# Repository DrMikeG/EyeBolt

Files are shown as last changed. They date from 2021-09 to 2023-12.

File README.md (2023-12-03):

# EyeBolt #

## 10th September 2023 ##
I've just captured the first full scan on the work driven turntable.
\EyeBolt\Mk5\Code\20_100StepTurnsTakingPictures\run_036

I'm now having a chat with chatGPT about the next steps:
```
`cv2.solvePnP()` is a function provided by the OpenCV library in Python for solving the Perspective-n-Point (PnP) problem, which is used in computer vision to estimate the pose (rotation and translation) of an object in a 3D space relative to a camera. This is precisely what you need when determining the extrinsic parameters between your camera and laser in your 3D scanner project.

Here's a more detailed explanation of how to use `cv2.solvePnP()`:

```python
import cv2
import numpy as np

# Define known 3D world points (object points)
object_points = np.array([
    [x1, y1, z1],
    [x2, y2, z2],
    # ... add more points ...
], dtype=np.float32)

# Define detected 2D image points
image_points = np.array([
    [u1, v1],
    [u2, v2],
    # ... add more points ...
], dtype=np.float32)

# Define camera matrix (intrinsic parameters), obtained from camera calibration
camera_matrix = np.array([
    [fx, 0, cx],
    [0, fy, cy],
    [0, 0, 1]
], dtype=np.float32)

# Define distortion coefficients if applicable (usually from camera calibration)
distortion_coeffs = np.array([k1, k2, p1, p2, k3], dtype=np.float32)

# Use cv2.solvePnP to estimate pose (extrinsic parameters)
retval, rotation_vector, translation_vector = cv2.solvePnP(object_points, image_points, camera_matrix, distortion_coeffs)

# 'retval' indicates the success of the solvePnP operation (usually 1 if successful)

# 'rotation_vector' is the rotation in Rodrigues form (axis-angle representation)
# Convert it to a rotation matrix if needed
rotation_matrix, _ = cv2.Rodrigues(rotation_vector)

# 'translation_vector' represents the translation of the object center in camera coordinates

# The resulting 'rotation_matrix' and 'translation_vector' represent the pose of the object
```

Key points to note:

- You need to provide `object_points`, which are the 3D coordinates of known points in the world coordinate system.
- `image_points` are the 2D coordinates of the corresponding points in the image.
- `camera_matrix` is the camera's intrinsic matrix, obtained through camera calibration.
- `distortion_coeffs` are the distortion coefficients, also obtained from camera calibration (may not always be needed).

The function returns the rotation vector (`rotation_vector`) and translation vector (`translation_vector`) that describe the pose of the object in relation to the camera.

You can then use the rotation and translation information to transform your laser line data from the camera's coordinate system to the world coordinate system, allowing you to align the laser data with your 3D point cloud.

Remember to make sure that your world points and image points are correctly matched and correspond to the same features in your images for accurate pose estimation. Additionally, if you have lens distortion, it's important to account for it using the distortion coefficients.
```

Measurements of box:
Camera focal plane to far wall distance = 315mm
11cm from far wall to pivot
Camera focal plane to pivot = 315mm - 110mm = 205mm
Blue laser source to camera axis - 92mm
Red laser source to camera axis - 92mm

Blue laser plane:
Origin (-92,0,0)
Direction ()
Vector in plane up far wall - from bottom to top of visible line
Vector in plane run from origin to 

## 4th September 2023 ##
Having mounted the df robot stepper with the 1:100 gearbox, I'm still struggling to get a consistent rotation.

Using the code in 19_QuarterTurnsTakingPictures I'm estimating the error by photographing each rotation and looking for the procession.

The closest I have so far is 1981 steps per revolution, which I still think might be ~2% to much

But the noise is annoying me now, so I'm going to stop.

## 22nd July 2023 ##

Capturing some light and dark rotations today to help debug the point cloud work I've been doing in Open3d (14_Open3d_Tut)

Try one capture after another, and looking at the light rotations, I think 128 steps is more than a full rotation. 122 seems much closer.

Also, my dark captures seem too dark now.

I've stated 15_Capture360_DarkOrLight to allow me to easily change between the new dark/light settings I am trying.

Still working on processing in Mk5\Code\14_Open3d_Tut\02_make_point_cloud_file.py
which can now:
- Make an undistorted light or dark frame video
- Make a side-by-side light and dark frame video (needs orientation to line up)
- Make a file containing point cloud coordinates from dark frames
- Display a point cloud using open3D

(The difference between light frames and dark frames is just me opening or closing the box... he he)

I'm not convinced by the settings in 
\EyeBolt\Mk5\Code\15_Capture360_DarkOrLight\my_camera_light.py
\EyeBolt\Mk5\Code\15_Capture360_DarkOrLight\my_camera_dark.py

Having some success processing light frames.

I should diagnose the turning issue by doing 1 photo per revolution for 10 revs...

## 13th July 2023 ##

Where are we up to?
I'm now capturing runs of cropped 950x950 images with low noise.
This took a lot of messing - but I'm very please with the result.

## 8th July 2023 ##

Because of the field of view, I don't care about much of the image.
Pico has limit - Max 150kb of data
Ideally I'd like 1.5mb for 900x900 at full resolution - but equally I don't care about most of the those pixels, only the red ones.

Most experiments with 2560x1440 at high compression (24)
Binning is automatically enabled when output size is less 1440, so wondered where many of my pixels went when I used small output.

The library I am using is really useful for setting the 100s of registers and capturing the output data.
But output size is set using an enum indexing into a table.

I didn't really want to abandoned the library, since its setting dozens of useful register values, but I want to use an output format that's not one of the pre-canned enum rows in the table.

The library itself is compiled into binary for efficiency, so I can't change it - but it turns out the table values are read-write so I can overwrite one row in the table.

I started off copying all the values from a working row, and setting the offsets to shuffle a cropped window along.

The camera works in two modes depending on the output size - so the values are used differently depending, which took me a while to figure out.

With a bit of trial and error, managed to shift the capture window the be 950x950 (without scaling?)

Capturing fewer pixels allowed me to lower the compression from 24 to 6 (very close to 5)

The next issue to address is the noise.
The library is very video-focused and doesn't expose any of the setting related to the auto-exposure or auto-gain controls.

Here I have to go to the data sheet and start messing with individual bits in registers.

My approach here was to set the camera to a known good state, take a photo, then adjust some experimental settings, and take a second photos and compare.

## 7th July 2023

Following other leads on long exposure:

https://forums.openmv.io/t/need-help-with-ov5640-exposure-timing/8238/5
https://forums.raspberrypi.com/viewtopic.php?t=350473

## 3rd July 2023 ##
Seem to have lost this link.
https://github.com/espressif/esp32-camera/issues/203

https://github.com/espressif/esp32-camera/blob/master/sensors/ov5640.c

## 2nd July 2023 ##

- If width is less than half of max width or height is less than half of max height then enable binning by setting _binning to be true
Further settings are the specified within _set_image_options()

- If width and height are equal to max width and max height then we don't need to scale, set _scale to false
- If width and height are equal to half max width and half max height then we don't need to scale if we using binning, set _scale to false
- Else we are using scaling:  `self._write_reg_bits(_ISP_CONTROL_01, 0x20, self._scale)` - this is using a mask to set the 5th bit

Other than the `_ISP_CONTROL_01 (0x5001) - # Bit[5]: Scale enable 0: Disable 1: Enable`
I don't see anything that sets scaling, and nothing uses the defined scaling registry addresses.

If you enable the value in this register, I think it must interpret the values X_OUTPUT_SIZE and Y_OUTPUT_SIZE differently.
X_OFFSET sn Y_OFFSET are used to define the copy before scaling and X_OUTPUT_SIZE and Y_OUTPUT_SIZE defined the scaled image size.

So, for the output size OV5640_SIZE_QHD (# 2560x1440)
h,      w,      mw,     mh,     sx, sy,     ex,     ey,     ox, oy, tx,     ty
2560,   1440,   2560,   1440,   0,  240,    2623,   1711,   32, 16, 2844,   1488, # QHD

```
self._binning = false # (1440 <= 1440 // 2) and (height <= max_height // 2)
self._scale = false # not ((true and true)

self._write_addr_reg(_X_ADDR_ST_H, 0, 240)
self._write_addr_reg(_X_ADDR_END_H, 2623, 1711)
self._write_addr_reg(_X_OUTPUT_SIZE_H, 2560, 1440)

self._write_addr_reg(_X_TOTAL_SIZE_H, 2844, 1488)
self._write_addr_reg(_X_OFFSET_H, 32, 16)

self._write_reg_bits(_ISP_CONTROL_01, 0x20, self._scale)
```

Thinking about moving away from jpeg again.
Example gif code:
``` 
frame = wait_record_pressed_update_display(True, cap)
    with open_next_image("gif") as f, gifio.GifWriter(
        f, cam.width, cam.height, displayio.Colorspace.RGB565_SWAPPED, dither=True
    ) as 
        ```

https://docs.circuitpython.org/en/latest/shared-bindings/gifio/index.html

file – Either a file open in bytes mode, or the name of a file to open in bytes mode.

width – The width of the image. All frames must have the same width.

height – The height of the image. All frames must have the same height.

colorspace – The colorspace of the image. All frames must have the same colorspace. The supported colorspaces are RGB565, BGR565, RGB565_SWAPPED, BGR565_SWAPPED, and L8 (greyscale)

The GIF frames are decoded into RGB565 big-endian format. displayio expects little-endian, so the example above uses Colorspace.RGB565_SWAPPED.

https://learn.adafruit.com/saving-bitmap-screenshots-in-circuitpython/overview
```
This guide introduces a CircuitPython library which is compatible with CircuitPython 5.0 and later. The library allows the programmer to take the pixels in a bitmap or on a screen and save them into standard 24 bits per pixel BMP files. Files may be on the CircuitPython USB flash filesystem (if it's set to writable mode) or onto a SD card.

To save bitmaps and screenshots you will need to add adafruit_bitmapsaver.mpy to the CIRCUITPY/lib directory.

save_pixels('/sd/pypaint.bmp', self._fg_bitmap, self._fg_palette)
```
http://paulbourke.net/dataformats/ppm/

## 1st July 2023 ##
In my v12 code to TweakCameraSettings I am using cam._write_register()

If I want to check current values I should try _read_register()

Looking at the internals we have a method on OV5640:
```
 def _set_size_and_colorspace(self) -> None:  # pylint: disable=too-many-locals
        
        # I am using  size=adafruit_ov5640.OV5640_SIZE_QHDA = 14  # 2560x1440
        size = self._size
        # [2560, 1440, _ASPECT_RATIO_16X9], # QHD
        # _ASPECT_RATIO_16X9 = const(4)
        width, height, ratio = _resolution_info[size]
        # _ratio_table = [
        #  mw,   mh,  sx,  sy,   ex,   ey, ox, oy,   tx,   ty
        #[2560, 1440, 0, 240, 2623, 1711, 32, 16, 2844, 1488],  # 16x9
        #]

        self._w = width     # 2560
        self._h = height    # 1440
        (
            max_width,      # 2560
            max_height,     # 1440
            start_x,        # 0
            start_y,        # 240
            end_x,          # 2623
            end_y,          # 1711
            offset_x,       # 32
            offset_y,       # 16
            total_x,        # 2844
            total_y,        # 1488
        ) = _ratio_table[ratio]

        self._binning = (width <= max_width // 2) and (height <= max_height // 2)
        self._scale = not (
            (width == max_width and height == max_height)
            or (width == max_width // 2 and height == max_height // 2)
        )

        self._write_addr_reg(_X_ADDR_ST_H, start_x, start_y)
        self._write_addr_reg(_X_ADDR_END_H, end_x, end_y)
        self._write_addr_reg(_X_OUTPUT_SIZE_H, width, height)

        if not self._binning:
            self._write_addr_reg(_X_TOTAL_SIZE_H, total_x, total_y)
            self._write_addr_reg(_X_OFFSET_H, offset_x, offset_y)
        else:
            if width > 920:
                self._write_addr_reg(_X_TOTAL_SIZE_H, total_x - 200, total_y // 2)
            else:
                self._write_addr_reg(_X_TOTAL_SIZE_H, 2060, total_y // 2)
            self._write_addr_reg(_X_OFFSET_H, offset_x // 2, offset_y // 2)

        self._write_addr_reg(_X_TOTAL_SIZE_H, total_x - 200, total_y // 2)
        self._write_addr_reg(_X_OFFSET_H, offset_x // 2, offset_y // 2)

        self._write_reg_bits(_ISP_CONTROL_01, 0x20, self._scale)
```
mw	2560				
mh	1440				
sx	0	_X_ADDR_ST_H			
sy	240	_X_ADDR_ST_H			
ex	2623	_X_ADDR_END_H			
ey	1711	_X_ADDR_END_H			
ox	32	_X_OFFSET_H	If not binning	16	_X_OFFSET_H
oy	16	_X_OFFSET_H	If not binning	8	_X_OFFSET_H
tx	2844	_X_TOTAL_SIZE_H	If not binning	2644	
ty	1488	_X_TOTAL_SIZE_H	If not binning	744	
scale	0	_ISP_CONTROL_01	0x20		

```
def _write_addr_reg(self, reg: int, x_value: int, y_value: int) -> None:
        self._write_register16(reg, x_value)
        self._write_register16(reg + 2, y_value)
```

There are two different window configurations, depending on if scaling is enabled.

The values above don't appear to make sense. What registers are they going into?

The OV5640 sensor has an image array of 2624 columns by 1964 rows
Of the 5,153,536 pixels, 5,038,848 (2592x1944) are active pixels and can be output. The other pixels are used for black 
level calibration and interpolation.

## 30th June 2023 ##
![manual](./readme_imgs/bit_packing_01.png)

The 8 bits of register 0x3821 control multiple things:
- jpeg enabled
- isp mirror
- sensor mirror
- horizontal binning

When setting the windowing, I will need to or in my additional bits.

The OV5640 using registers 0x3800 -> 0x3814 for image windowing.
(but maybe not all the bits)

| Address    | Register Name     | Default Value | Description                             |
|------------|-------------------|---------------|-----------------------------------------|
| OX3800     | TIMING HS         | 0x00          | X address start high byte[ll:8] high byte |
| OX3801     | TIMING HS         | 0x00          | X address start low byte[7:0] low byte |
| OX3802     | TIMING VS         | 0x00          | Y address start high byte[10:8] high byte |
| OX3803     | TIMING VS         | 0x00          | Y address start low byte[7:0] low byte |
| OX3804     | TIMING HW         | 0x0A          | X address end high byte[11:8] high byte |
| OX3805     | TIMING HW         | 0x3F          | X address end low byte[7:O] low byte |
| OX3806     | TIMING VH         | 0x07          | Y address end high byte[10:8] high byte |
| OX3807     | TIMING VH         | 0x9F          | Y address end low byte[7:O] low byte |

DVP - Digital video port parallel output interface
```The Digital Video Port (DVR) provides 10-bit parallel data output in all formats supported and extended features including 
compression mode, HSYNC mode, CClR656 mode, and test pattern output. The DVP is also used to receive the video 
data from an external camera, which will be sent out through the OV5640 MIPI interface. ```

| OX3808     | TIMING DVPHO      | 0x0A          | DVP output horizontal width[ll:8] high byte|
| OX3809     | TIMING DVPHO      | OX20          | DVP output horizontal width[7:0] low byte |
| OX380A     | TIMING DVPVO      | OX07          | DVP output vertical height[10:8] high byte |
| OX380B     | TIMING DVPVO      | OX98          | DVP output vertical height[7:0] low byte |
| OX380C     | TIMING HTS        | 0x0B          | Total horizontal size[ll high byte |
| OX380D     | TIMING HTS        | 0x1C          | Total horizontal size[7:0] low byte |
| OX380E     | TIMING VTS        | 0x07          | Total vertical size[1 5:8] high byte |
| OX380F     | TIMING VTS        | 0xB0          | Total vertical size[7:0] low byte |
| OX3810     | TIMING HOFFSET    | 0x00          | ISP horizontal offset[ll :8] high byte |
| OX3811     | TIMING HOFFSET    | 0x10          | ISP horizontal offset[7:0] low byte |
| OX3812     | TIMING VOFFSET    | 0x00          | ISP vertical offset[10:8] high byte  |
| OX3813     | TIMING VOFFSET    | 0x04          | ISP vertical offset[7:0] low byte  |

From the manual:

+------------------+--------------+-----------+------------------------------------+----------------+
|      Format      | Resolution   | Frame Rate|         Scaling Method             |  Pixel Clock   |
+------------------+--------------+-----------+------------------------------------+----------------+
|    5 Mpixel      |  2592X1944   |   15 fps  |   Full resolution (dummy 16 pixels, |   96/192 MHz   |
|                  |              |           |   horizontal, 8 lines)             |                |
+------------------+--------------+-----------+------------------------------------+----------------+
|    1280X960      |  1280X960    |   45 fps  |   2608x1952 with dummy              |   96/192 MHz   |
|                  |              |           |   subsampling in vertical and       |                |
|                  |              |           |   horizontal                        |                |
+------------------+--------------+-----------+------------------------------------+----------------+
|    1080P         |  1920X1080   |   30 fps  |   1296X968                          |   96/192 MHz   |
+------------------+--------------+-----------+------------------------------------+----------------+
|    720P          |  1280X720    |   60 fps  |   Supports 2x2 binning              |   96/192 MHz   |
+------------------+--------------+-----------+------------------------------------+----------------+
|    VGA           |  640X480     |   90 fps  |   Cropping from full resolution     |   48/96 MHz    |
|                  |              |           |   (1936x1088 with dummy pixels)     |                |
+------------------+--------------+-----------+------------------------------------+----------------+
|    QVGA          |  320X240     |   120 fps |   Cropping 2592x1944 to 2560x1440   |   24/48 MHz    |
|                  |              |           |   Subsampling in vertical and       |                |
|                  |              |           |   horizontal                        |                |
+------------------+--------------+-----------+------------------------------------+----------------+

## 29th June 2023 ##
Using code 11 I tried lots of different camera settings. There were better and worse settings, but none of them I would say were good, and there were lots of errors.
The errors might be the result of me changing the settings to frequently.

## 15th June 2023 ##
Lets look at how I could capture higher quality in less memory.

https://docs.python.org/3/c-api/buffer.html#bufferobjects

## 4th June 2023 ##
Adding SD card to camera module to aid calibration.

I want high quality images - going to try writing from camera to SD card.

06_ will mix together 04_largeBitmapCapture with protoMicroSDWithMotor.

Additional libs:
adafruit_sdcard.mpy which I've taken from adafruit-circuitpython-bundle-7.x-mpy-20230325

Saving images at SXGA (1280x1024)
Quality - Controls the JPEG quality.  Valid range is from 2..55 inclusive

Quality 4
1280 1024
327680
Traceback (most recent call last):
  File "code.py", line 193, in <module>
  File "code.py", line 164, in main
MemoryError: memory allocation failed, allocating 327680 bytes

## 24th May 2023 ##
Camera calibration

Give me an overview of how to perform OpenCV's cv2.calibrateCamera function.
https://docs.opencv.org/4.x/dc/dbb/tutorial_py_calibration.html

Instead of chess board, we can alternatively use a circular grid. In this case, we must use the function cv.findCirclesGrid() to find the pattern. Fewer images are sufficient to perform camera calibration using a circular grid.

https://longervision.github.io/2017/03/18/ComputerVision/OpenCV/opencv-internal-calibration-circle-grid/

## 23rd May 2023 ##

Micro SD cards.

I can't keep sending image data across the serial terminal - it's madness. Maybe once I have the processing algorithm dialed in I can put it back on the pico, but to start with, I think I want to capture a load of full res- images.

I plan to add a micro SD card reader to the pico.
I had one in my box of bits, but it was a generic one, which didn't look like it could use `sdcardio`.

I bought an Adafruit MicroSD Card breakout+ (P254)
https://www.adafruit.com/product/254

This has the DI and DO pins, so I should be able to follow this guide: https://learn.adafruit.com/adafruit-micro-sd-breakout-board-card-tutorial/circuitpython

I don't so the pi pico on the list, so cannot verify that it supports sdcardio. If it does not, I will try using adafruit_sdcard instead.

Wiring: https://learn.adafruit.com/adafruit-micro-sd-breakout-board-card-tutorial/arduino-wiring

Because SD cards require a lot of data transfer, they will give the best performance when connected up to the hardware SPI pins.

SPI Example
To setup a SPI bus, you specify the SCK, MOSI (microcontroller out, sensor in), and MISO (microcontroller in, sensor out) pins. 
The Pico uses a different naming convention for these:

SPIx_SCK = SCK
SPIx_TX = MOSI
SPIx_RX = MISO
So use that mapping to help find available pins.

import board
import busio
spi = busio.SPI(clock=board.GP2, MOSI=board.GP3, MISO=board.GP4)

This clashes with the pins I've used for the motor so far, so I will need to re-prototype that.

Connect the 5V pin to the 5V pin on the Arduino
Connect the GND pin to the GND pin on the Arduino

Connect (Brown) CLK to pin 13 SCK (SPIx_SCK) clock=board.GP2
Connect (Orange) DO to pin 12 MISO (SPIx_TX) MISO=board.GP4
Connect (Yellow) DI to pin 11 MOSI (SPIx_RX ) MOSI=board.GP3
Connect (Green) CS to pin 10 (you will also need a fourth pin for the 'chip/secondary select' (SS))

`Go to the beginning of the sketch and make sure that the chipSelect line is correct, for this wiring we're using digital pin 10 so change it to 10!`
`Use 8.3 format for file names`

Soldered up the wires and connecting to a pico on a protoboard.
Copied across library adafruit_sdcard.mpy which I've taken from adafruit-circuitpython-bundle-7.x-mpy-20230325

Edited the file list example into \Mk5\Code\protoMicroSD - run it and listed the files on the SD card.

Next test is to write a file - and generate unique filename in 8.3

I have to move the motor now too, as that was overlapping with the SPI pins.
I don't think it needed to.

```
import board
import busio
import sdcardio
import storage
# Use the board's primary SPI bus
spi = board.SPI()
# Or, use an SPI bus on specific pins:
#spi = busio.SPI(board.SD_SCK, MOSI=board.SD_MOSI, MISO=board.SD_MISO)

# For breakout boards, you can choose any GPIO pin that's convenient:
cs = board.D10
```

Another quick experiment in \Mk5\Code\protoMicroSDWithMotor

Moved motor pins to 6,7,8 & 9. This works, but that now clashes with 7,8 & 9 being used by the camera!

I've managed to move to the motor to 22,26,27 & 28.

That leaves my GP6 free for E-brake, and maybe 0 and 1 - but I never like using them.

## 30th April 2023 ##

First light?

OV5640_COLOR_RGB = 0
OV5640_COLOR_YUV = 1
OV5640_COLOR_GRAYSCALE = 2
OV5640_COLOR_JPEG = 3
https://github.com/adafruit/Adafruit_CircuitPython_OV5640/blob/main/adafruit_ov5640.py

OV5640_SIZE_96X96 = 0  # 96x96
OV5640_SIZE_QQVGA = 1  # 160x120
OV5640_SIZE_QCIF = 2  # 176x144
OV5640_SIZE_HQVGA = 3  # 240x176
OV5640_SIZE_240X240 = 4  # 240x240
OV5640_SIZE_QVGA = 5  # 320x240
OV5640_SIZE_CIF = 6  # 400x296
OV5640_SIZE_HVGA = 7  # 480x320
OV5640_SIZE_VGA = 8  # 640x480
OV5640_SIZE_SVGA = 9  # 800x600
OV5640_SIZE_XGA = 10  # 1024x768
OV5640_SIZE_HD = 11  # 1280x720
OV5640_SIZE_SXGA = 12  # 1280x1024
OV5640_SIZE_UXGA = 13  # 1600x1200
OV5640_SIZE_QHDA = 14  # 2560x1440
OV5640_SIZE_WQXGA = 15  # 2560x1600
OV5640_SIZE_PFHD = 16  # 1088x1920
OV5640_SIZE_QSXGA = 17  # 2560x1920

https://github.com/adafruit/Adafruit_CircuitPython_BitmapSaver
https://learn.adafruit.com/circuitpython-display-support-using-displayio/bitmap-and-palette

https://cdn-learn.adafruit.com/assets/assets/000/118/553/thumb100square/adafruit_products_img0006.jpg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

## 19th April 2023 - Mark V progress ##

I've been working on this perhaps more than I realise.
So, a quick video to capture the changes.

I set out to test the camera - which means wiring up the camera board.
But before did that, I decided I wanted to test the other features of the board, which in this design means control of the turn table.

I start out with the parts I stripped out of the mark 4.
I used the Tb6612 motor control board, with the beefy 12volt nema 17 motor.

I made a timing belt driven system where a 20 tooth gear on the motor drives a 400 tooth belt around the outside of this 3d printed turntable.
This gives me 1800 steps per revolution - but it was noisy and a bit rough.

In the previous design I had one motor turning a pair of chunk lead screws - pushing assemblies along a pair of linear rails. It needed some grunt.

But here, I'm just spinning a table in free space - no grunt needed. So i've switch down a litte 5v 28BYJ geared stepper. This gives me 512 steps be revolution and is buttery smooth and silent.

In other news, I've started to mount the components in their box.

I'm just 3d printing frame sections, that clip over the rim of the box, and align the content to be vertical.

Here I have the camera board and pico mounted on a protoboard (which is not yet wired) And I have the Powell lense laser tacked on the end.

I'm thinking I should make the turn table attach to this, to make a single unit, rather than fixing it to the box. This would make allow me to make a CAD model of the whole assembly, rather than try to measure it accurately.

Not sure about that yet.

Next steps? Well, Now I've proven I can drive the turn table, I should start wiring up nthe camera and try to get a first image.

Nema 17 = 200 steps per revolution
20 tooth cog, so 10 steps per tooth.
Driving a 180 tooth table, to 1800

## 14th April 2023 - Stepper trouble ##
I'm reducing the number of stepper motors from 2 to 1.
I only need a motor to driver the turntable.

I've made a motor and table assembly with a 400 tooth 2gt timing belt. Small gear has 20 teeth and large gear has 180.

I'm struggling to get any motor to run smoothly and reliably. I've switch out motor driver boards and nema 17 motors. It's all very rattly.

Since there is almost no load on this motor, I'm considering switching down to a tiny 28byj-48, 5V stepper.

https://microcontrollerslab.com/28byj-48-stepper-motor-raspberry-pi-pico-micropython/

https://forums.adafruit.com/viewtopic.php?f=19&t=117680

I also found a suggestion for diagnosing the control lines, so I might try that first too.

## 10th April 2023 - Wiring up camera protoboard ##
I have a protoboard for the pico from Monk makes

![PICO PROTO PCB](./readme_imgs/monk.jpg)

Which seems perfect for this wiring job. I have the camera on via a socket and the pico soldered directly on board.

I have a 5v 3v3 and Gnd rail, and the camera pins are broken out onto columns, which should make is easy for me to solder them.

My next question, is do I have 5 spare pins for the motor board?

Whilst I print test-support pieces to interface the camera board and the prototboard, I'm thinking about the new turn table:

https://avtehnik.github.io/gt2-gear-genaretor/

Using a 140 tooth turntable, using a belt length tool:

https://www.technobotsonline.com/timing-pulley-distance-between-centres-calculator.html

140 on larger PCD (dp) 89.127
20 on smaller PCD (dp) 12.732
Distance between centers 113.577
Belt length 400mm

## 8th April 2023 - Start of the Mark V ##

Adafruit OV5640 Camera Breakout - 120 Degree Lens
https://learn.adafruit.com/adafruit-ov5640-camera-breakout/raspberry-pi-pico-usage

Camera connections
For the Raspberry Pi Pico setup shown in these examples, wire the following connections:

OV5640 GND to Pi Pico GND
OV5640 3V to Pi Pico 3V3
OV5640 SDA to Pi Pico GP8
OV5640 SCL to Pi Pico GP9
OV5640 HS to Pi Pico GP21
OV5640 VS to Pi Pico GP7
OV5640 XC to Pi Pico GP20
OV5640 PC to Pi Pico GP11
OV5640 D2..D9 to Pi Pico GP12..GP19
OV5640 RT to Pi Pico GP10

The pull-up resistors shown on GP8 and GP9 are not required for Adafruit's OV5640 camera break-out board but may be required for other camera breakout boards.

![Alt text](./readme_imgs/adafruit_products_5673-fb.jpg)

![Alt text](./readme_imgs/adafruit_products_pico-camera-lcd_bb.png)

The camera module requires a well-regulated 3.3v supply in order to operate.

**G (GND):** Connect to microcontroller GND

**3V (3.3V):** Connect to microcontroller +3.3V supply

PD (powerdown): Optional connection to microcontroller GPIO. When pulled HIGH the camera module is put into power-down mode. When released or pulled LOW the camera is powered on. This pin can also be pulsed HIGH as a way to reset the camera.
RT (reset): Optional connect to microcontroller GPIO. Pull the pin LOW to reset the camera module and release it or pull it HIGH to enter operating mode.
Both pins have built-in pull resistors, so by default the camera is powered on and allowed to exit reset mode.

The camera module must be configured using I2C.

**SDA:** Connect to microcontroller SDA

**SCL:** Connect to microcontroller SDL

**XC (external clock)**: When the XCLK jumper is set to "EXT" (the default), this pin must be driven with a 24MHz square wave from the microcontroller or other source. When the jumper is changed to "INT", then an on-board clock generator is used instead. In this case, the XC pin should not be driven by the microcontroller and may be left unconnected.

**PC (pixel clock)** tells the microcontroller when image data is available. This may need to be connected to a specific microcontroller pin.

**VS and HS** are synchronization signals, which tell the microcontroller when a new frame (VS) or row (HS) of data begins. These may need to be connected to specific microcontroller pins.

The 8 data pins (numbered from **D2 to D9** because reasons) carry data out of the camera into the microcontroller.

Depending on mode, these 8 data bits can be half of a 16-bit pixel value, or one byte of JPEG data.

```If your microcontroller has a 2x9 header available, that method is strongly preferred! The high speed signals of the camera module can be scrambled even with short lengths of jumper wire on a solderless breadboard.```

xclk, pclk, vsync, href: Free choice of any pin
reset, shutdown: Free choice of any pin. Can omit one or both, but the initialization sequence is less reliable.
data_pins: Any 8 sequential pins in GPIO ordering (e.g., GPIO2..GPIO9).

https://learn.adafruit.com/adafruit-ov5640-camera-breakout/ascii-mirror-dem

## 1st April 2023 - The End of the Mark IV ##

This project has been on pause for a while, whilst I've done other things - but it's very literally always there - taking up space in my study.

This is the Mark 4 - it's a laser beam scanner. There are a pair of synchronized lead-screws, which move the laser and the sensor horizontally along these sturdy linear tracks.

The subject is placed on a linear rotary turntable. Combing the movement of the laser sensor with the 2 degrees of freedom of the table, you can gather 3D data from the occlusion of the data.

Both the table and the lead screws are driven by Nema steppers, the lead screws are synchronized via timing belts, and the turntable is driven via a 3d printed gear pair. Stepper driver boards are controlled by a pico, which coordinates the movement with the sensing.

I've got this built out as far as calibration - and partly looking at those results I've decided not to take this build any further.

The problems are:

1) Too many movement parts.
There's too much slop in the system. Just calibrating this with m2 machine screws, I'm seeing 1mm of inaccuracy on the position, which isn't going to give me the results I want.

2) Too big.
I was a little ambitious with my scan volume
I was limited height-wise by by my turntable design
I was limited length-wise by not wanting to cut up the lead screws and linear rails.
So I build this into this big crate - which isn't something I want to have hanging around (like it has for the past year).

## 11th September 2022 ##

Something I was reader referred to circuitPython AsyncIO - which I don't think was a thing back when I started this project 2 years ago.

This isn't preemptive multi-tasking, but cooperative. You can't break into the event loop following an interrupt, but one task can cede control (let other tasks run) when it is waiting (e.g time.sleep)

This might be a good way forward for me, to try and keep the motor movement fluid. At the moment there are sleep statements in every motor step.

Potentially I could be checking the abort button and the laser sensor whilst the motors are paused.

I'm going to have a play with tis code in Mk4\Code\AsyncIO\Prototype01\code.py

Guide here: <https://learn.adafruit.com/cooperative-multitasking-in-circuitpython-with-asyncio>

```
# SPDX-FileCopyrightText: 2022 Dan Halbert for Adafruit Industries
#
# SPDX-License-Identifier: MIT

import asyncio
import board
import digitalio

async def blink(pin, interval, count):
    with digitalio.DigitalInOut(pin) as led:
        led.switch_to_output(value=False)
        for _ in range(count):
            led.value = True
            await asyncio.sleep(interval)  # Don't forget the "await"!
            led.value = False
            await asyncio.sleep(interval)  # Don't forget the "await"!
        # These tasks finish whenever the for-loop expires

async def main():
    led1_task = asyncio.create_task(blink(board.D1, 0.25, 10))
    led2_task = asyncio.create_task(blink(board.D2, 0.1, 20))

    await asyncio.gather(led1_task, led2_task)  # Don't forget "await"!
    print("done")

asyncio.run(main())
```

What about sharing memory between tasks?

```
# SPDX-FileCopyrightText: 2022 Dan Halbert for Adafruit Industries
#
# SPDX-License-Identifier: MIT

import asyncio
import board
import digitalio
import keypad

class Interval:
    """Simple class to hold an interval value. Use .value to to read or write."""

    def __init__(self, initial_interval):
        self.value = initial_interval

async def monitor_interval_buttons(pin_slower, pin_faster, interval):
    """Monitor two buttons: one lengthens the interval, the other shortens it.
    Change interval.value as appropriate.
    """
    # Assume buttons are active low.
    with keypad.Keys(
        (pin_slower, pin_faster), value_when_pressed=False, pull=True
    ) as keys:
        while True:
            key_event = keys.events.get()
            if key_event and key_event.pressed:
                if key_event.key_number == 0:
                    # Lengthen the interval.
                    interval.value += 0.1
                else:
                    # Shorten the interval.
                    interval.value = max(0.1, interval.value - 0.1)
                print("interval is now", interval.value)
            # Let another task run.
            await asyncio.sleep(0)

async def blink(pin, interval):
    """Blink the given pin forever.
    The blinking rate is controlled by the supplied Interval object.
    """
    with digitalio.DigitalInOut(pin) as led:
        led.switch_to_output()
        while True:
            led.value = not led.value
            await asyncio.sleep(interval.value)

async def main():
    interval1 = Interval(0.5)
    interval2 = Interval(1.0)

    led1_task = asyncio.create_task(blink(board.D1, interval1))
    led2_task = asyncio.create_task(blink(board.D2, interval2))
    interval1_task = asyncio.create_task(
        monitor_interval_buttons(board.D3, board.D4, interval1)
    )
    interval2_task = asyncio.create_task(
        monitor_interval_buttons(board.D5, board.D6, interval2)
    )

    await asyncio.gather(led1_task, led2_task, interval1_task, interval2_task)

asyncio.run(main())
```

This is perhaps a better way to go? Using countio as a layer over interupts?

```
import asyncio
import board
import countio

async def catch_interrupt(pin):
    """Print a message when pin goes low."""
    with countio.Counter(pin) as interrupt:
        while True:
            if interrupt.count > 0:
                interrupt.count = 0
                print("interrupted!")
            # Let another task run.
            await asyncio.sleep(0)

async def main():
    interrupt_task = asyncio.create_task(catch_interrupt(board.D3))
    await asyncio.gather(interrupt_task)

asyncio.run(main())
```

Inside the interrupt, I'd want to know the current value of X, and have someone to stash it.
We could clear and reset the values for each sweep.

Here main() is run with asyncio - I think I would need other tasks
Task per sweep?

## 6th September 2022 ##

A long line - but not too long.

Powell lenses are laser line generator lens that can fan out collimated beams in one dimension. They have the shape of a prism with a rounded roof, and are often used to transform a narrow laser beam into a uniformly illuminating line. 

If it has a 60 degree beam angle from a 7mm aperture, then at 30cm the beam length is huge.
If I reduce the aperture to 2.6mm then I should get around a 10cm line length at 30cm throw.

## 26th August 2022 ##
Calibrating using the long edge of the L-shaped print.

Zeroing X out at 0
Zeroing X (from 0)
Loop 0 of 10
Detect changed at 1800
Detect changed at 5650
Detect changed at 5630
Detect changed at 1780
Loop 1 of 10
Detect changed at 1800
Detect changed at 5650
Detect changed at 5630
Detect changed at 1780
Loop 2 of 10
Detect changed at 1800
Detect changed at 5650
Detect changed at 5630
Detect changed at 1780
Loop 3 of 10
Detect changed at 1800
Detect changed at 5650
Detect changed at 5630
Detect changed at 1770
Loop 4 of 10
Detect changed at 1800
Detect changed at 5660
Detect changed at 5640
Detect changed at 1780
Loop 5 of 10
Detect changed at 1810
Detect changed at 5660
Detect changed at 5690
Detect changed at 5710
Detect changed at 5640
Detect changed at 1780
Loop 6 of 10
Detect changed at 1800
Detect changed at 5650
Detect changed at 5640
Detect changed at 1780
Loop 7 of 10
Detect changed at 1810
Detect changed at 5650
Detect changed at 5630
Detect changed at 1780
Loop 8 of 10
Detect changed at 1800
Detect changed at 5660
Detect changed at 5700
Detect changed at 5710
Detect changed at 5630
Detect changed at 1780
Loop 9 of 10
Detect changed at 1800
Detect changed at 5650
Detect changed at 5630
Detect changed at 1780
Done!

Detect changed at 1800	1800	1800	1800	1800	1800	1810	1800	1810	1800	1800	1802	
Detect changed at 5650	5650	5650	5650	5650	5660	5660	5650	5650	5660	5650	5653	3851
Detect changed at 5630	5630	5630	5630	5630	5640	5640	5640	5630	5630	5630	5633	
Detect changed at 1780	1780	1780	1780	1770	1780	1780	1780	1780	1780	1780	1779	3854

Between 38.51 and 38.4mm
Measures 39.8

## 21st August 2022 ##

Have been away for two weeks. Just before I left I was working on calibrating the leadscrew movement.

After discovering I could focus the laser - I now need to determine if it's better to focus on the object or the sensor.

Using \Code\Operating\BeamMovementCalibrate\code3.py

```
I estimate 30mm to be an average of 2770 steps

I think the lead-screw is 2mm for 20 teeth
I think the belt drive is 1:1
The motor is 200 steps per revolution
30mm should be 3000 steps
01mm should be 100 steps
I this suggests the fuzz (region of uncertainty) at each end of my block is 1.15mm

Lengths in mm:
27.7
27.7
27.7
27.7
27.7
27.7
27.6
27.6
27.6
27.5
27.6
27.6
27.7
27.7
27.7
27.7
27.7
27.7
27.8
27.8
Measured length 29.84mm

Error (end to end): 
+/- 2.34
+/- 2.04

Happy with this, and the consistent movement in steps of 10 - how can it be improved?

Is there an offset or a reduction I'm not aware off?
It is the beam width? Can I just compensate for that? Does it always measure small?
```

Running again for 15mm block, whilst I print a 25x40mm block

1351 steps (13.5mm)

01mm should be 100 steps
15mm should be 1500 steps
less because there is an area of uncertainty

On the way back, the numbers as consistently lower, suggesting I could run a pass in both directions and take an average!
How to group the readings when they are s

## 29th July 2022 ##

I've just made a measurement of the number of stepper motor steps needed to complete one table revolution.

I put a pin in the table, so that it broke the beam twice per revolution.
I measure the number of steps in each of the 4 states, and averaged to calculate steps per revolution.

I did two runs with the beam at different positions, to get different length quarters

|blockedA|openA|blockedB|openB|sum        |
|--------|-----|--------|-----|-----------|
|28      |319  |39      |2071 |2457       |
|28      |404  |11      |2051 |2494       |
|27      |404  |13      |2044 |2488       |
|25      |416  |15      |2037 |2493       |
|24      |434  |18      |2030 |2506       |
|22      |422  |21      |2029 |2494       |
|20      |428  |22      |2027 |2497       |
|19      |429  |19      |2029 |2496       |
|20      |428  |18      |2029 |2495       |
|20      |430  |15      |2031 |2496       |
|19      |432  |19      |2024 |2494       |
|19      |437  |19      |2021 |2496       |
|17      |439  |21      |2018 |2495       |
|20      |447  |20      |2014 |2501       |
|12      |450  |22      |2009 |2493       |
|17      |449  |20      |2008 |2494       |
|18      |449  |20      |2003 |2490       |
|19      |455  |20      |2001 |2495       |
|20      |456  |22      |2002 |2500       |
|15      |465  |19      |1997 |2496       |
|18      |463  |17      |1999 |2497       |
|15      |467  |18      |1997 |2497       |
|        |     |        |     |2495.571429|

|blockedA|openA|blockedB|openB|sum        |
|--------|-----|--------|-----|-----------|
|11      |1139 |19      |1330 |2499       |
|19      |1139 |12      |1330 |2500       |
|13      |1139 |12      |1330 |2494       |
|19      |1139 |12      |1316 |2486       |
|19      |1141 |14      |1330 |2504       |
|16      |1140 |13      |1328 |2497       |
|15      |1140 |14      |1327 |2496       |
|15      |1142 |13      |1329 |2499       |
|14      |1138 |13      |1327 |2492       |
|15      |1146 |9       |1329 |2499       |
|15      |1142 |13      |1325 |2495       |
|18      |1140 |12      |1327 |2497       |
|15      |1143 |13      |1324 |2495       |
|17      |1142 |14      |1325 |2498       |
|15      |1142 |15      |1323 |2495       |
|15      |1144 |13      |1327 |2499       |
|14      |1143 |13      |1324 |2494       |
|12      |1145 |15      |1323 |2495       |
|14      |1148 |15      |1322 |2499       |
|10      |1145 |18      |1324 |2497       |
|        |     |        |     |2496.368421|

The gear ratio was designed to be 0.0800 

The motor has a step angle of 1.8deg
360 / 1.8 = 200 steps per revolution.

1.0 / 0.08 = 12.5

200 * 12.5 = 2500.

So the predicted number of steps for a revolution is 2500
The measured is ~2495
If I do 100 sample angles (sounds like a lot) that gives 25 steps per chunk, which feels enough to be accurate without backlash.

## 8th July 2022 ##

I have made a number of modifications to the drive - but I had troubles with the new motor.

The drive speed needed changing, and the wiring colours have changes. I used a breakboard to switch around the wires, having used the trick of spinning the motor by hand and shorting the pairs, to find when the resistance increases.

![Alt text](./readme_imgs/servo_rewire.png)

I have changed from a single belt (with tensioning) to two belts on a double drive gear.

## 11th Jun 2022 ##

### Gearbox ###
Working out a small gear box for the new table design

http://hessmer.org/gears/InvoluteSpurGearBuilder.html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

https://evolventdesign.com/pages/gear-ratio-calculator

Number of Teeth: Input Gear: 20 (16mm diameter)
Number of Teeth: Gear 2:    80 (54mm diameter)
Number of Teeth: Gear 3:    24 (30mm diameter)
Number of Teeth: Gear 4:    75 (80mm diameter)

Gear Ratio:	0.0800

Input Speed:	200
Output Speed:	16.0000

Gears 1 & 2
http://hessmer.org/gears/InvoluteSpurGearBuilder.html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

Gears 3 & 4
http://hessmer.org/gears/InvoluteSpurGearBuilder.html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

![Alt text](./readme_imgs/gears1_2_params.png)
![Alt text](./readme_imgs/gears3_4_params.png)

## Thumbstick ##

I felt like I needed more inputs/controls as I develop the Mk4.

Now that I have more travel, I want to be able to set limits for the scan region (to save time not scanning empty space)

The obvious input formats are up-confirm down-confirm to set the limits of the table (for the height of the part) and left-confirm right confirm to set the limits for the max extent of the part when rotated.

To avoid this input being an awkward series of switch presses, I decided to try and integrate a thumbstick.

The thumbstick from the sensor kit says 5v on the silk screen, but seems to work just fine on 3v3.
It has two analogue outs, which I feed into 26 and 27 (ADC ins on the pico) and a switch which I connect to 22 because it is nearby.

I'm not using the analogue values, only a less than 25% or more than 75% to detect left or right - else it gives no input.

![Alt text](./readme_imgs/thumbA.png)
![Alt text](./readme_imgs/thumbB.png)

I wired it up on a breadboard with a test sketch - then soldered connectors onto the main pico shield.
22, 26 & 27 were thankfully unused. I also spliced on the power lines to the existing 3v3 and ground rows.

I had a bit of trouble wiring 22,26 & 27 and in the end I didn't get the colouring consistent on the thumbstick end and pico end (green and white are swapped).

### Nema no more ###

I thought my old motor might have been:
```Nema 14 Bipolar 1.8deg 5Ncm (7.08oz.in) 0.4A 10V 35x35x20mm 4 Wires```

But it turns out it is probably a:
```Stepper motor - NEMA-17 size - 200 steps/rev, 12V 350mA 20 N*cm,```

My driver (Adafruit TB6612) can handle 1.2A

So I've ordered:

```Nema 17 Bipolar Stepper 1.8deg 12v 1.2A 400mN.m 42x42x40mm 4-wires Nema17 CNC```

This hybrid bipolar Nema 17 stepper motor with 1.8 degree step angle (200 Steps / Revolution).
Manufacturer Part Number: 17HS3001-20B
Motor Type: Bipolar Stepper
Step Angle: 1.8 degree
Holding Torque: 400 mN.m
42.3mm*42.3mm*L40mm

New motor will only be x2 as strong (not x8) but still better. Plus it's a drop in replacement.
I might chose a smaller drive gear. This will mean less tooth contact, but less speed and torque multiplier.

## Mark 3 ##

Starting planning the next major redesign of the scanner - planning on going back to optical - but combination optical/mechanical using occlusion not Time Of Flight.

## KY-008 ##

https://arduinomodules.info/ky-008-laser-transmitter-module/

This module consists of a 650nm red laser diode head, a resistor and 3 male header pins. Handle with caution, do not point the laser beam directly to the eyes.

Operating Voltage	5V

Connect the module signal pin (S) to pin 13 on the Arduino and ground (-) to GND.

The middle pin on the module is not used.

## Receiver ##
Laser Receiver Sensor Module non-modulator Tube Pi Arduino Pic Lazer

The laser receiver sensor module uses a non-modulated laser receiver to detect the laser signal.

For use indoors where there is no light, sunlight or other sources of light which will interfere with the sensor, recommended for use in dark environments.

![Alt text](./readme_imgs/s-l1600.jpg)
 
Voltage : 5v
Output high level when receive laser signal
Output low level when not receive laser signal
Size : 1.5cm x 1.9cm

https://www.codrey.com/electronic-circuits/the-mysterious-laser-receiver-sensor-module/

```
A cryptic 3-pin sensor?
The 3-pin sensor is actually a minuscule light sensor (receiver) diode with an integrated amplifier and an open-collector transistor at its output. Output of the module, designed to operate on 5VDC power supply, can only go low (L), and the open-collector transistor inside the 3-pin sensor can sink about 20mA current. The description “non-modulator tube” actually points the fact that the light sensor can handle any source of light and it’s not like a 3-pin  infrared sensor module (TSOP1838 for example) that only detects an infrared pulse train within a particular frequency band.

...the sensor is known in China as “ISO203 Laser Receiver”. You can see its pin notation in the image provided below.
```

![Alt text](./readme_imgs/sensor2.png)

![Alt text](./readme_imgs/20220330_133722.jpg)
This is going to be so cool!

https://matplotlib.org/stable/gallery/mplot3d/voxels_rgb.html

After dealing with an issue where the ends of the arms bounce after the beginning and end of the stroke, I could start some calibration scans.

![Alt text](./readme_imgs/2022_04_15.gif)

## 9th March 2022 ##

Hit various problems with boundary tracing.
Firstly, had to reduce tracing to 4-connected from 8-connected
Then remove small regions,

Now, with my new spring can scan, I have a boundary on level rev_i == 3 where the path crosses itself:

![Alt text](./readme_imgs/2022_09_03_01.png)

| Chunk  | N     | Steps       | diff |
|----|------|--------|---|
| 71 | 12   | 852   |   |
| 36  | 13   | 458     |   |
| 1  | 13.3 | 13.3   |   |
|108 |      | 1333.3 | 0 |

108
54
27

### Hat Scans ###

![Alt text](./readme_imgs/hat.gif)

![Alt text](./readme_imgs/hatMeasure.gif)

![Alt text](./readme_imgs/sorting_hat_point_cloud.png)

![Alt text](./readme_imgs/2022_09_03_01.png)

![Alt text](./readme_imgs/HatMinBool.png)

## 30th Sept 2021 ##

Push buttons have too much spring.
Can I get a photo interupter to work?
KY-10 <https://arduinomodules.info/ky-010-photo-interrupter-module/>

Connect the power line (middle) and ground (left) to +5V and GND respectively. Connect signal (S) to pin 3 on the Arduino.

Operating Voltage 3.3 ~ 5V

- (left) GND
middle +5V
S (right) Pin 3

```
int Led = 13; // define LED pin
int buttonpin = 3; // define photo interrupter signal pin
int val; //define a numeric variable

void setup()
{
 pinMode(Led, OUTPUT); // LED pin as output
 pinMode(buttonpin, INPUT); //photo interrupter pin as input
}

void loop()
{
 val=digitalRead(buttonpin); //read the value of the sensor 
 if(val == HIGH) // turn on LED when sensor is blocked 
 {
  digitalWrite(Led,HIGH);
 }
 else
 {
  digitalWrite(Led,LOW);
 }
}
```

### Gear Ratio ###

80 : 12
360 / 1.8 = 200 steps per revolution.

200 / 12 = 16.66667
16.66667 * 80 = 1333.33

My measured estimate was 1331
Leap-step every 3 revolutions

## 26th Sept 2021 ##

Going back to gear design for turntable.

<http://hessmer.org/gears/InvoluteSpurGearBuilder.html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>

## 21st September 2021 ##

After a few days of folly with a beautiful planetary gear train, I've rigged up some linear rail and a servo with a crank arm to move the pointer.

I now need to operate the servo.

MG 995

Signal pin (Orange pin) -The PWM signal which states the axis position is given through this pin.
VCC (Red pin) - Positive power supply for servo motor is given to this pin.
Ground(Brown pin) - This pin is connected to ground of circuit or power supply.

Operating voltage range: 4.8 V to 7.2 V
Rotational degree: 180º
Dead band width: 5 μs
Operating temperature range: 0ºC to +55ºC
Current draw at idle: 10mA
No load operating current draw: 170mA
Current at maximum load: 1200mA

<https://ceilingnote.blogspot.com/2021/05/raspberry-pi-pico11-control-servo-motor.html>

<https://learn.adafruit.com/circuitpython-essentials/circuitpython-servo>

How to list the pins:

```
import board
dir(board)
```

```import board
dir(board)
```

## 18th September 2021 ##

My VL53L3CX Arrived today!

With the improved detection accuracy, the sensor features a 25~3000mm sensing range, automatic smudge correction, and glass cross-talk immunity.

Typical full FoV 25°

Boo!

Got to design a different measuring,

If the radius of a circle is 70mm,
The total circumference is 440mm
100 degrees would be
(100 / 360) * 440 = 122mm
I only need ~70mm of travel, so a standard servo should be ok with a serious fan gear

So - my thoughts.
I'm giving up on doing this optically for now - I'm going to try and make a touch sensor using a servo and a momentary switch.

I have reservations about the travel I'll need for a physical measurement.

Also, there's no reason the measured object is going to stay still.

Need something 

VL53L3CX Time-Of-Flight ToF Ranging Sensor Module Breakout 3Meter 940Nm...
(Estimated delivery: Wed 15 Sep - Thu 23 Sep)

According to the VL53L0X datasheet:
> During the ranging operation, several VCSEL infrared pulses are emitted, then reflected back by the target object, and detected by the receiving array.

VCSEL is Vertical cavity surface emitting laser. Therefore I would say a pulse laser.

## VL6180X ##

VL6180X VL6180 Range Finder Optical Ranging Sensor Module for Arduino
(Estimated delivery: Wed, 08 Sep - Thu, 09 Sep)

Three-in-one smart optical module
Proximity sensor
Ambient Light Sensor
VCSEL light source
Fast, accurate distance ranging
Measures absolute range from 0 to above 10 cm (ranging beyond 10cm is dependent on conditions)
an handle about 5mm to 200mm of range distance.

850 nm

The field or view of VL6180X is approximately ±12.5°

FOV for the IR laser used for the distance sensor is 25 degrees (+/- 12.5). This means the spot size (the area over which the sensor reads a distance) is about 0.4 times the distance from the sensor. At a distance of 50 mm, it returns a reading from some point within a 20 mm spot on the object. Good for a proximity detector, not so good if you are trying to find the edge of an object.

`Don't forget to remove the protective cover off the sensor, it may be a clear or slightly tinted plastic!`

Resolution: 1 mm2

### Connecting up ###

<http://arduinolearning.com/code/arduino-and-vl6180x-module-circuitpython-example.php>

<https://learn.adafruit.com/adafruit-vl6180x-time-of-flight-micro-lidar-distance-sensor-breakout/pinouts>

Vin - this is the power pin. Since the chip uses 2.8 VDC, we have included a voltage regulator on board that will take 3-5VDC and safely convert it down. To power the board, give it the same power as the logic level of your microcontroller - e.g. for a 5V micro like Arduino, use 5V

GND - common ground for power and logic

SCL - I2C clock pin, connect to your microcontrollers I2C clock line.
SDA - I2C data pin, connect to your microcontrollers I2C data line.

GPIO - this is a pin that is used by the sensor to indicate that data is ready. It's useful for when doing continuous sensing.
Note there is no level shifting on this pin, you may not be able to read the 2.8V-logic-level voltage on a 5V microcontroller (we could on an arduino UNO but no promises). Our library doesn't make use of this pin but for advanced users, it's there!

I'm going to solder this up to a 5 pin connector.

And at the pico end...

To setup an I2C bus, you specify the SCL and SDA pins being used. You can look for "SCL" and "SDA" in the pin names in the pinout diagram above.

I2Cx_SCL = SCL
I2Cx_SDA = SDA
For example, here is how you would setup an I2C bus to use GP1 as SCL and GP0 as SDA:

```
import board
import busio

i2c = busio.I2C(scl=board.GP1, sda=board.GP0)

import board
import busio
import adafruit_vl6180x
i2c = busio.I2C(board.SCL, board.SDA) // Does not work on the pico
sensor = adafruit_vl6180x.VL6180X(i2c)

```

Next you'll need to install the Adafruit CircuitPython VL6180X library on your CircuitPython board.

Remember for non-express boards like the, you'll need to manually install the necessary libraries from the bundle:

adafruit_vl6180x.mpy
adafruit_bus_device
Before continuing make sure your board's lib folder or root filesystem has the adafruit_vl6180x.mpy, and adafruit_bus_device files and folders copied over.

Next connect to the board's serial REPL so you are at the CircuitPython >>> prompt.

## Steppers ##

<https://thepihut.com/products/raspberry-pi-pico> (3v logic)

Can it drive a nema stepper directly? Nope.

Can I use one of the 2 Adafruit motor shield v2.3 I have handy? Nope.

<https://learn.adafruit.com/adafruit-feather-rp2040-pico/pinouts>

Adafruit DRV8833

<https://learn.adafruit.com/use-dc-stepper-servo-motor-solenoid-rp2040-pico?view=all>

I've just gotten hold of one of these:

Adafruit TB6612 1.2A DC/Stepper motor Driver
<http://adafru.it/2448> <https://learn.adafruit.com/adafruit-tb6612-h-bridge-dc-stepper-motor-driver-breakout>

Power Pins

Vmotor - This is the voltage for the motors, not for the logic level. Keep this voltage between 4.5V and 13.5V. This power supply will get noisy so if you have a system with analog readings or RF other noise-sensitive parts, you may need to keep the power supplies seperate (or filtered!)

Vcc - this is the voltage for the logic levels. Set to the voltage logic you'll be using on your microcontroller. E.g. for Arduinos, 5V is probably what you want. Can be 2.7V to 5.5V so good for 3V or 5V logic

GND - This is the shared logic and motor ground. All grounds are connected

Signal in Pins
These are all 'Vcc logic level' inputs
INA1, INA2 - these are the two inputs to the Motor A H-bridges
PWMA - this is the PWM input for the Motor A H-bridges, if you dont need PWM control, connect this to logic high.
INB1, INB2 - these are the two inputs to the Motor B H-bridges
PWMB - this is the PWM input for the Motor B H-bridges, if you dont need PWM control, connect this to logic high.
STBY - this is the standby pin for quickly disabling both motors, pulled up to Vcc thru a 10K resistor. Connect to ground to disable.

Motor Out Pins
These are 'Vmotor level' power outputs

Motor A - these are the two outputs for motor A, controlled by INA1, INA2 and PWMA
Motor B - these are the two outputs for motor B, controlled by INB1, INB2 and PWMB

<https://learn.adafruit.com/adafruit-tb6612-h-bridge-dc-stepper-motor-driver-breakout/using-stepper-motors>

We'll wire it to a Metro, but you can use any microcontroller you like!

Connect:

Vmotor to 12V (red wire)
Vcc to 5V (orange wire)
PWMA and PWMB to Vcc (orange wire)
GND to ground
AIN2 to Digital 4
AIN1 to Digital 5
BIN1 to Digital 6
BIN2 to Digital 7

Motor: Then hook one stepper motor coil to Motor A (red and yellow) and the second coil to Motor B (green and gray/brown). If you have another motor, you'll need to experiment a little to figure out which wires are which coil. Check any documentation you have! You can use a multimeter to measure between wires, the ones with a small resistance between them are a pair to a coil, for example. If the motor is vibrating but not spinning, check all wires are connected and try flipping around a pair or rechecking the wire pairs.

<https://learn.adafruit.com/adafruit-tb6612-h-bridge-dc-stepper-motor-driver-breakout/python-circuitpython>

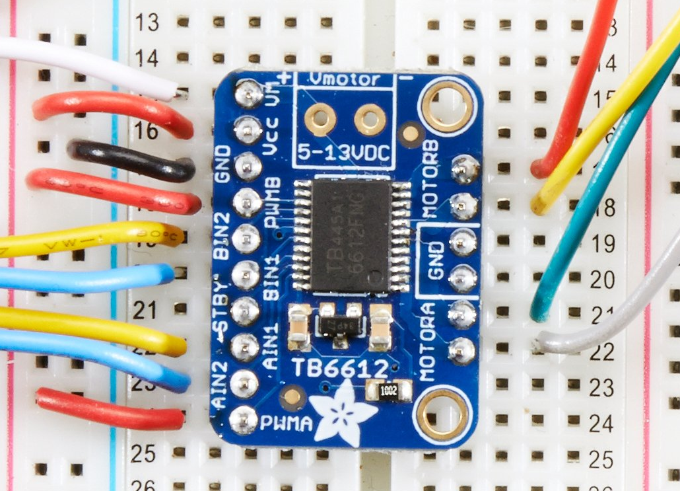
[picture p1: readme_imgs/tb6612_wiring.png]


I plan to power the motor with my soldering iron power lead (+many other used lead) which is 12V 2A tip positive.

The short black power socket lead I have is also wired red to `tip positive` to red lead, so that's easy to remember.

The motor looks to be the easy part.

Does it matter if its a 9v or 12V stepper I wonder?

### Putting circuit on the pico ###

Booted pico with bootSelect held down.

Downloaded, and dropped adafruit-circuitpython-raspberry_pi_pico-en_US-6.3.0.uf2 onto device rp2

It reappears as circuitpy (E:)

I already have Mu installed (awful IDE, but handy)

I need the adafruit motor library.
Downloaded the library bundle from <https://circuitpython.org/libraries>

Copied adafruit_motor into E:\lib

```
The DRV8833 motor controller can control the two motor coils inside the stepper motor (think of it like a circular bucket brigade passing the power around A-B-A-B-A-B and so on) by receiving signals from four digital output pins on the Pico.

Wire it up as shown in the diagram here:
```

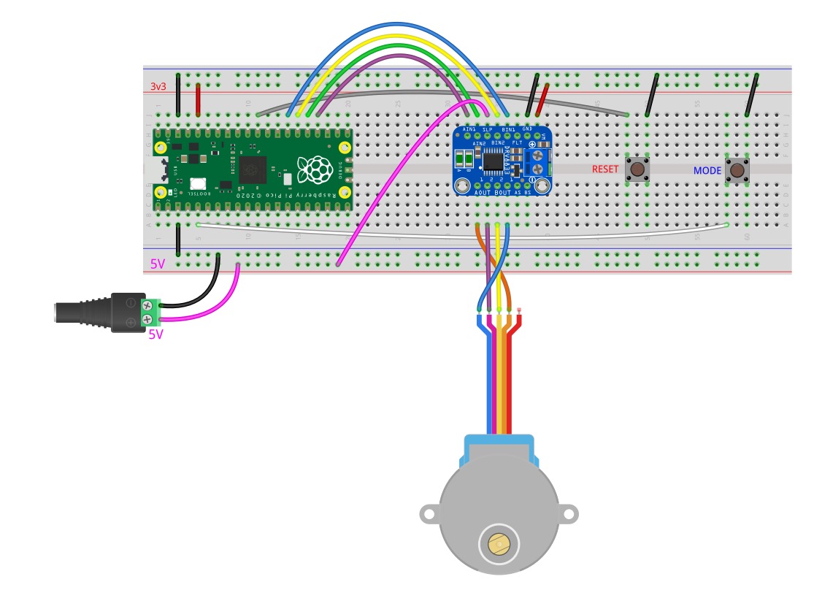
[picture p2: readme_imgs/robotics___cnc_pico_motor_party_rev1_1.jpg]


Pico

```
Pico pin 27 (GP21)  to driver pin BIN1
Pico pin 26 (GP20) to driver pin BIN2
Pico pin 25 (GP19) to driver pin AIN2
Pico pin 24 (GP18) to driver pin AIN1

Pico GND to driver GND
Pico 3v3 to driver VM
```

Nema 14 Bipolar 1.8deg 5Ncm (7.08oz.in) 0.4A 10V 35x35x20mm 4 Wires

- Ship from: Germany 14HS08-0404S

360 / 1.8 = 200 steps per revolution.

### Micro switches ###

<https://simonprickett.dev/buttons-and-leds-with-micropython-for-pi-pico/>
Pull up example allowing my to use ground pins not the poor 3.3V...

Circuit python does not support interrupts?

```
"""
Button example for Pico. Prints message to serial console when button is pressed.

REQUIRED HARDWARE:
* Button switch on pin GP13.
"""
import time
import board
import digitalio

button = digitalio.DigitalInOut(board.GP13)
button.switch_to_input(pull=digitalio.Pull.DOWN)

while True:
    if button.value:
        print("You pressed the button!")
        time.sleep(0.5)
```

I plan on using blah and blah pins for input.

#ß## Logging ###

<https://learn.adafruit.com/getting-started-with-raspberry-pi-pico-circuitpython/data-logger>

Now that I can take measurements and turn the motors, the next step is to write the values out somewhere...

```
CircuitPython does not allow your computer to write to the filesystem at the same time as CircuitPython is writing to the filesystem. Therefore, if you simply run storage.remount("/", readonly=False) in boot.py, CIRCUITPY is no longer writable by your computer, which means you cannot write to or delete files from the CIRCUITPY drive. This means you cannot modify boot.py. To return the filesystem to a state writable by your computer, you would need to run some commands in the REPL. More information on this process is available at the end of this page.
```

Remounts the given path with new parameters.

Parameters
readonly (bool) – True when the filesystem should be readonly to CircuitPython.

```
"""
boot.py file for Pico data logging example. If pin GP0 is connected to GND when
the pico starts up, make the filesystem writeable by CircuitPython.
"""
import board
import digitalio
import storage

write_pin = digitalio.DigitalInOut(board.GP0)
write_pin.direction = digitalio.Direction.INPUT
write_pin.pull = digitalio.Pull.UP

# If write pin is connected to ground on start-up, CircuitPython can write to CIRCUITPY filesystem.
if not write_pin.value:
    storage.remount("/", readonly=False)
```

```
"""
Data logging example for Pico. Logs the temperature to a file on the Pico.
"""
import time
import board
import digitalio
import microcontroller

led = digitalio.DigitalInOut(board.LED)
led.switch_to_output()

try:
    with open("/temperature.txt", "a") as datalog:
        while True:
            temp = microcontroller.cpu.temperature
            datalog.write('{0:f}\n'.format(temp))
            datalog.flush()
            led.value = not led.value
            time.sleep(1)
except OSError as e:  # Typically when the filesystem isn't writeable...
    delay = 0.5  # ...blink the LED every half second.
    if e.args[0] == 28:  # If the filesystem is full...
        delay = 0.25  # ...blink the LED faster!
    while True:
        led.value = not led.value
        time.sleep(delay)
```

to keep it still whilst I jab at it, and maybe use gravity to reduce the force require to trip the switch?

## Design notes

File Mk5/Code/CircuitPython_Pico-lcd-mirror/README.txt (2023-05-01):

This bundle contains two folders, one each for CircuitPython 7.x and CircuitPython 8.x. You must use the files that match the version of CircuitPython you're using, e.g. if you are using CircuitPython 7, you will copy the files from the CircuitPython 7.x folder to your CIRCUITPY drive.
To use this project bundle, simply copy the contents of the CircuitPython version folder you're using from the zip file to your CIRCUITPY drive.
Contents in each version include:
* the code.py file
* the lib/ folder and all of its contents (including subfolders and .mpy or .py files)
* any assets (such as images, sounds, etc.)
NOTE: This will replace the current code.py, and the lib folder and its contents. Back up any desired code before copying these files!
 This zip was downloaded from https://learn.adafruit.com/adafruit-ov5640-camera-breakout/lcd-mirror-demo-2 on April 30, 2023.

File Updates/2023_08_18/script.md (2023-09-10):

Update

I had to go back and remind myself what I last shared about this project.

I showed the new turntable based on the 28BYK

I showed the capturing first light with the OV5640.

I showed the open CV calibration of the OV5640.

I can't believe I've not showed anything since then!?

I did a load of work, and intended to make a video of progress - but then didn't.
Instead I've been waiting for parts, which have all just arrived.

So, in this video I will bring us up to date with progress, and mention the new parts, and then I will dive into try to capture scans with the new parts, and figuring out what the next set of challenges are.

# EyeBolt #
 
Because of the field of view, I don't care about much of the image.
Pico has limit - Max 150kb of data
Ideally I'd like 1.5mb for 900x900 at full resolution - but equally I don't care about most of the those pixels, only the red ones.
 
Most experiments with 2560x1440 at high compression (24)
Binning is automatically enabled when output size is less 1440, so wondered where many of my pixels went when I used small output.
 
The library I am using is really useful for setting the 100s of registers and capturing the output data.
But output size is set using an enum indexing into a table.
 
I didn't really want to abandon the library, since its setting dozens of useful register values, but I want to use an output format that's not one of the pre-canned enum rows in the table.
 
The library itself is compiled into binary for efficiency, so I can't change it - but it turns out the table values are read-write so I can overwrite one row in the table.
 
I started off copying all the values from a working row and setting the offsets to shuffle a cropped window along.
 
The camera works in two modes depending on the output size - so the values are used differently depending, which took me a while to figure out.
 
With a bit of trial and error, managed to shift the capture window the be 950x950 (without scaling?)
 
Capturing fewer pixels allowed me to lower the compression from 24 to 6 (very close to 5)
 
The next issue to address is the noise.
The library is very video-focused and doesn't expose any of the setting related to the auto-exposure or auto-gain controls.
 
Here I have to go to the data sheet and start messing with individual bits in registers.

I like working with micro controllers because you can flash it fresh everytime.
When I get raspberry pi projects working, im never 100% sure I could repeat the process.
And I like working if python because the source is on the device. There is never a question if which compiler or libraries you used - because you can look and there they are.
Bit even with the ability to reset and trace what's going on, there is still the opportunity to be fooled by the things.

My approach here was to set the camera to a known good state, take a photo, then adjust some experimental settings, and take a second photos and compare.

Tried a setting to control something, and it made an amazing difference to the noise level.
Commited immediately.
Tried it again. Rubbish again.
Realised the sun had moved around and I had gotten up and shut the curtain.
Reducing the background light had changed the automatic exposure and or the automatic gain control.
So then I decided to turn off the automatic gain and exposure controls. this also seems to resolve the image corruption  or maybe not. This still catches me out.

So now I can capture a reasonble low noise image, will minimal compression, cropping it to the region of interest

Run_016.mp4 - hat spinning in box
Run_019.mp4 - hat spinning in box - white background

These are low res pictures, being taken slowly by the pico.
I'm stitching them together to make essentially a timelapse video.
In between each image, the motor advances the turn table.

Exposure testing with the red laser line.

Run 23 - testing different background illuminated exposure settings
Run 24 - testing different in box exposure settings

Best setting I could find were : run_024_exp_minus3.mp4

Pretty big deal:
Run_69 R2D2 in dark, lit by laser. 
Cropped image -much higher resolution & lower compression.

Distortion corrected.
Run 70 - different exposure

run_074_x_run_075.mp4 - hat scan, comparing exposure in the box to ambient.

In the day light image, I have much

Video of scan as point cloud - very noisy!

run_077_x_run_078.mp4 - R2 scan, comparing exposure in the box to ambient.

To reduce internal reflections and scatter, I've lined key parts of the box with the adhesive vinyl. 

run_079.mp4 - deck of cards scan - start of calibration.
Not calibrated in X/Y or Z!

I'm going to need more data! To average out reflectance noise, and also because the incident angle of the laser is not optimal for all surface positions.
The simplest way I could think to do this, is to add a second laser of another color. Although it turns out these are much harder to source than the red lasers.

I'd like to do a colour scan too - how would that work?

Well the pixels we use to know the shape are clearly obscured by the colour of the laser.
But once we know where the surface point is in 3D space, we should be able to look in another image, work out which new pixel represents that point on the surface, and sample a colour from that pixel from there.

Now the biggest obstacle I have to this is my turn table, which I noticed when making looping scan videos, does not rotate 360 degrees. In fact, it doesn't even reliably rotate.

I hadn't heard good things about the little 28BYK steppers, but it was so much simpler than having to build a gear box on a nema motor.
I spent a while sketching out designs for indexed gear and geneva drive - but it was hard to miniaturize as I wanted.

My approach for now is to swap to what I ope is a better motor.

This tiny DF Robot FIT0503 Micro Metal Geared Stepper Motor

I can use 3d printed adaptors to pop it in place of the 28BYK.

It has less backlash, and from these early experiments looks to step in much more reliable increments.

So, now I've

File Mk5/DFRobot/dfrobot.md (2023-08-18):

I have a new tiny motor to try.

DF Robot FIT0503 Micro Metal Geared Stepper Motor

4 wired

INTRODUCTION
This is a miniature stepper motor with 100:1 metal reduction gear box for enhanced torque. It has a voltage input range of 5 - 12V DC. This product is suitable for the 3D printers and applications which require precise rotation control.

Note: Please limit the motor current, or overlarge current will burn the motor.

SPECIFICATION
Stepper Motor:
Coil resistance: 30Ω±10%
NO. Of Phases: 2 PHASES
Step Angle: 18° / Step
MAX.Starting Frequency: 900PPS min
MAX.Slewing Frequency: 1200 PPS min
Pull IN Torque: 6gf-cm min
Lead Out Torque: 10gf-cm max

Stepper Motor with Gear Box:
Step Angle: 18/100° / Step
MAX.Starting Frequency: 900PPS min
MAX.Slewing Frequency: 1200 PPS min
Pull IN Torque: 0.5Kgf-cm min
Lead Out Torque: 0.8Kgf-cm max
Cable Length: 15cm
Weight: 14g

Red Line: B
White Line: B-
Yellow: A
Black: A-

Motor board out to motor in.

White A    Yellow
Blue  A-   Black       
Red   B    Red
Green B-   White
Black (G)

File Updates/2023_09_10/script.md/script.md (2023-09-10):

The last update on this project was about a month ago, at which point I had swapped the motor on my direct drive turn table.

I was using a 28BYJ stepper, which had terrible backlash, and a lack of usable rotation positions.
I switched it up to this smaller FIT0503 Micro Metal Geared Stepper Motor.

This has a precision metal gear box with a 1:100 reduction.

Because it was smaller than the motor it was replacing, I could just print some shims to fit it into the exiting mechanism.

When I installed this, there was noticeably less backlash for the table, and many more steps per revolution.

But I noticed immeidatley, that using the published number of steps per revolution, the turn table wasn't turning a full revolution.

So, it was time to determine the number of steps empirically.

So the experiemnt setup is to run capture and image, and then perform a full revolution of the table, an to repeat this a number of times. When viewed as a timelapse video, the sequence of images should show stationary image, but and under or over rotation will be represented as procession or recessions in the frames.

The data sheet step angle is 18 degrees, so 20 steps per revolution of the motor shaft. With a 1:100 gear box, that becomes 2000 steps per revolution. This sequence of images (which is looping) show that for 1984 steps is one that one full revolution of the table.

For this sequence we reduced the steps between captures from 1984 to 1976, and now the table is under rotating.

Not being able to position the table accuratley was where we started, and whilst it has improved witht he new motor, the number of steps per revolution 1981 is almost a prime number, and therefore difficult to divide into even steps.

I took a bit of a break, and decided that what I wanted to do was redesign the turn table to be more fit for purpose.   

In the new design I'm now using the same motor, but rather than directly driving the table, I am using a special work gear.

The table has 100 teeth around the outside, which correspond to 100 diffent orientation positions.
 
 The new table is very slow - but it gives exact ly 100 fixed rotation positions.
 Moving from one rotation position to the next requires 1981 steps of the motor, and the position is locked for about 500 of the steps, so the stepper and gearbox can easily afford to be off by +/- 20 steps, as long the error is cyclic not cumulative.

Now, with 200 steps per tooth and 100 steps per revolution, it takes the table almost 3 hours to do 10 revolutions. This sequence of image shows the stability of the period of the new table design.

And yes, I did just chuck whatever junk I had to hand onto the table at the start of this experiment.

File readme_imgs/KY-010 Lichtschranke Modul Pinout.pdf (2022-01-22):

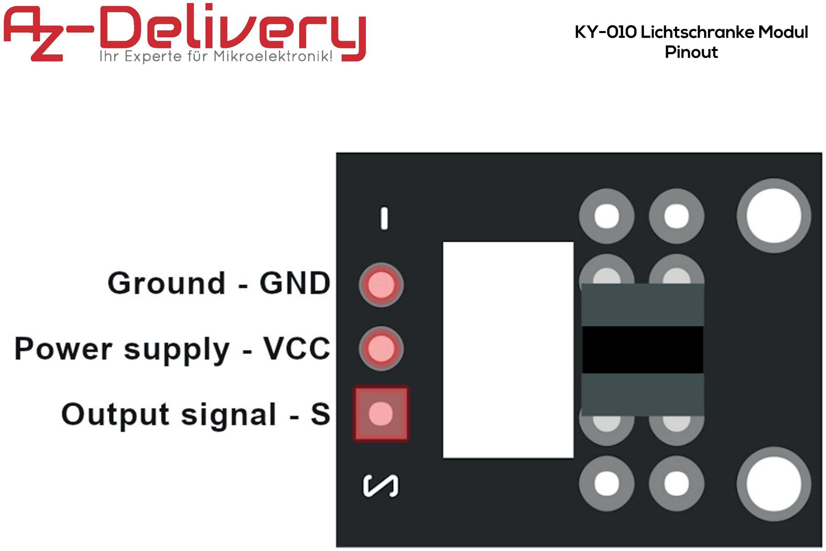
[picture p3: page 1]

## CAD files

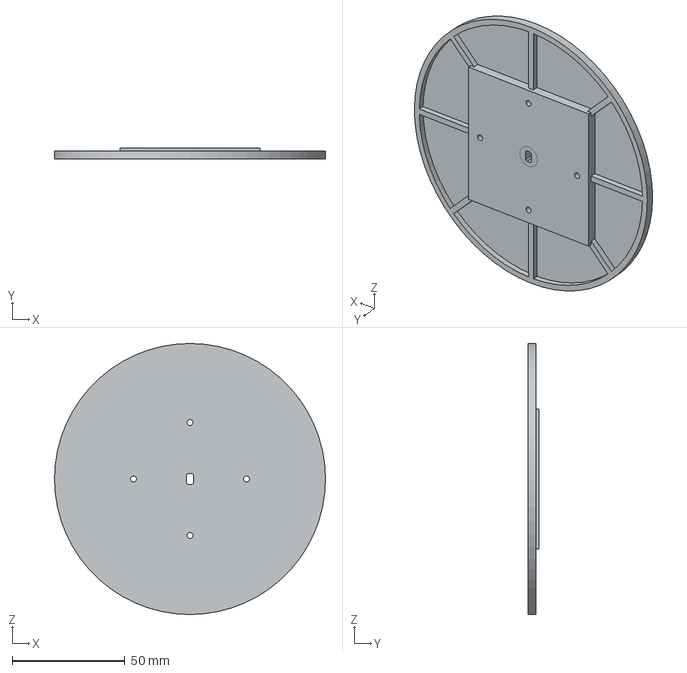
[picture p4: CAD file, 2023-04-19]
Mk5/28BYJ/DirectDriverTable3.stp
120.0 x 5.00 x 120.0 mm

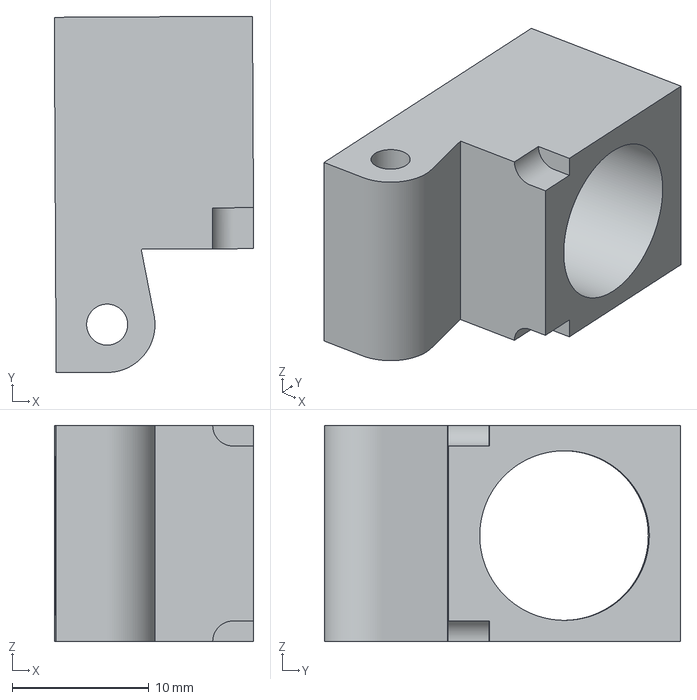
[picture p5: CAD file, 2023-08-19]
Mk5/BoxClips/hinges/lazer_holder_red_angle_06.3mf
14.6 x 26.1 x 15.8 mm

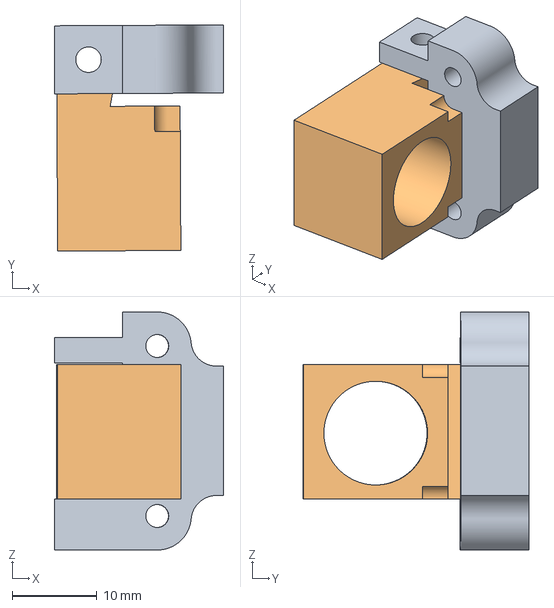
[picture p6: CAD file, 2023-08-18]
Mk5/BoxClips/lazer_holder_blue_angle_05.3mf
19.9 x 26.6 x 28.0 mm
lazer_holder_blue_angle_05 x 2

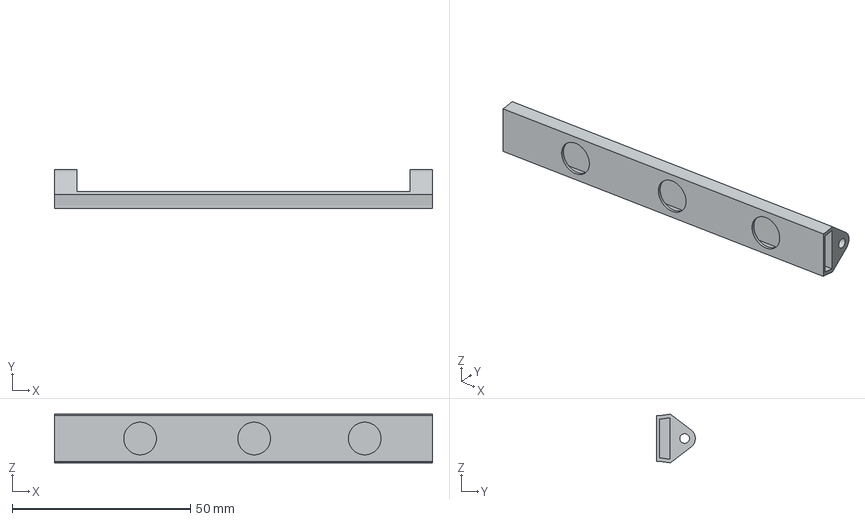
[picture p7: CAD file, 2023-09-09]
Mk5/BoxClips/lights/LED_Strip_trough_02.3mf
106.0 x 10.9 x 13.7 mm

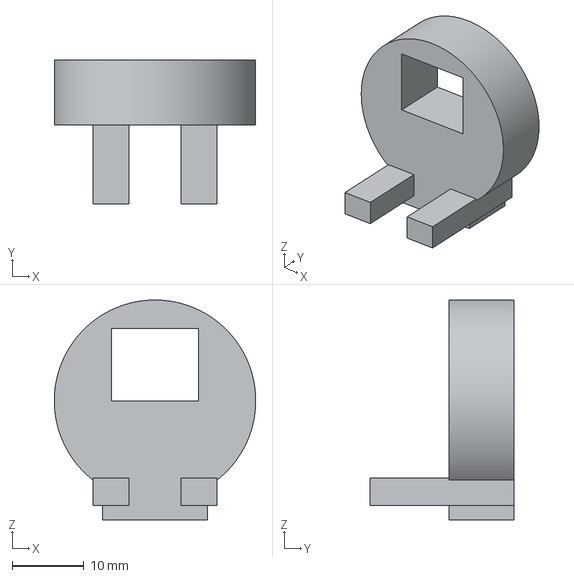
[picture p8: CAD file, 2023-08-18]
Mk5/DFRobot/BoxConnectedMotorAdaptor03.3mf
28.0 x 20.0 x 30.6 mm

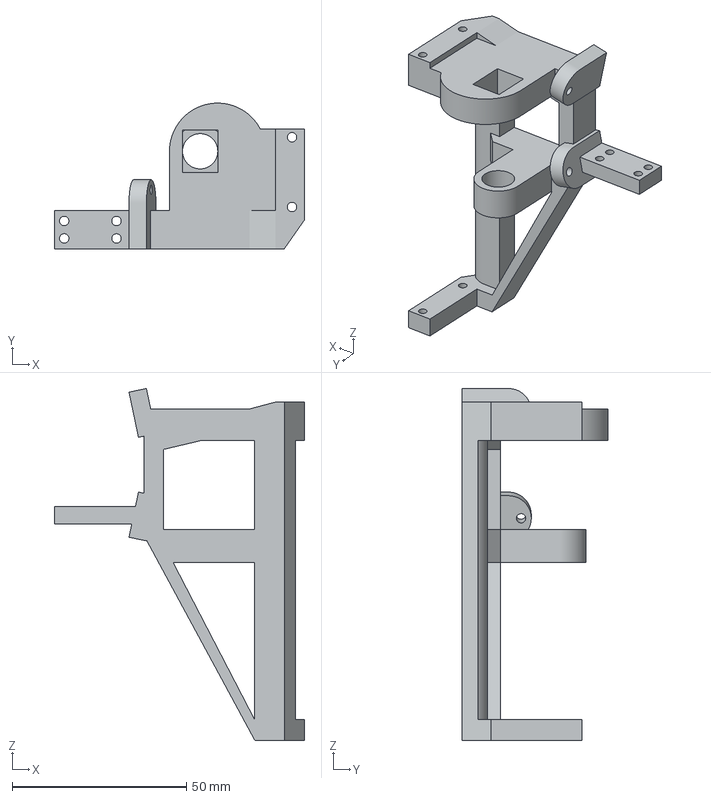
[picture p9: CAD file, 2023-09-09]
Mk5/DFRobot/Rotary01/gear_support/RollerBearingSupport2.3mf
71.7 x 41.8 x 100.9 mm

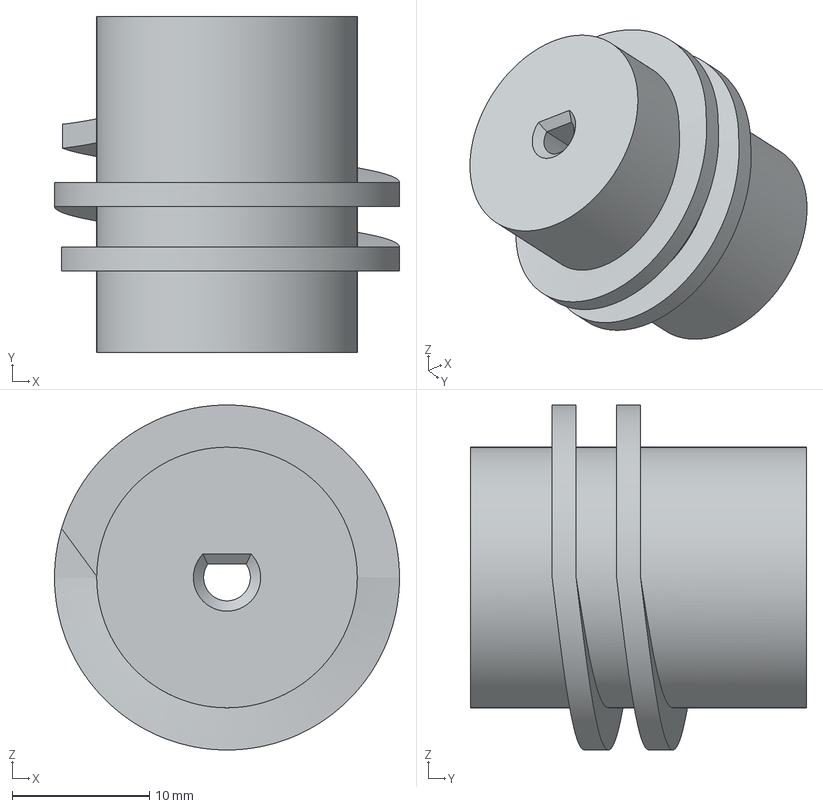
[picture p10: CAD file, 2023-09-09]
Mk5/DFRobot/Rotary01/Rotary04_WormGearPrint06.3mf
25.1 x 24.5 x 25.1 mm

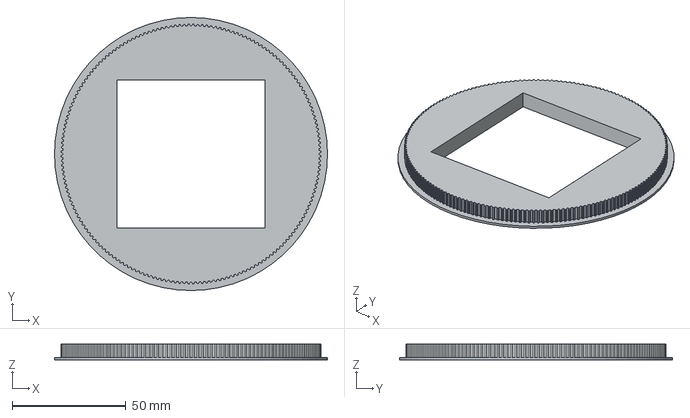
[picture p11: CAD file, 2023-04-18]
Mk5/gt2/180_teeth_lip_cutout_01.stp
120.0 x 120.0 x 7.00 mm

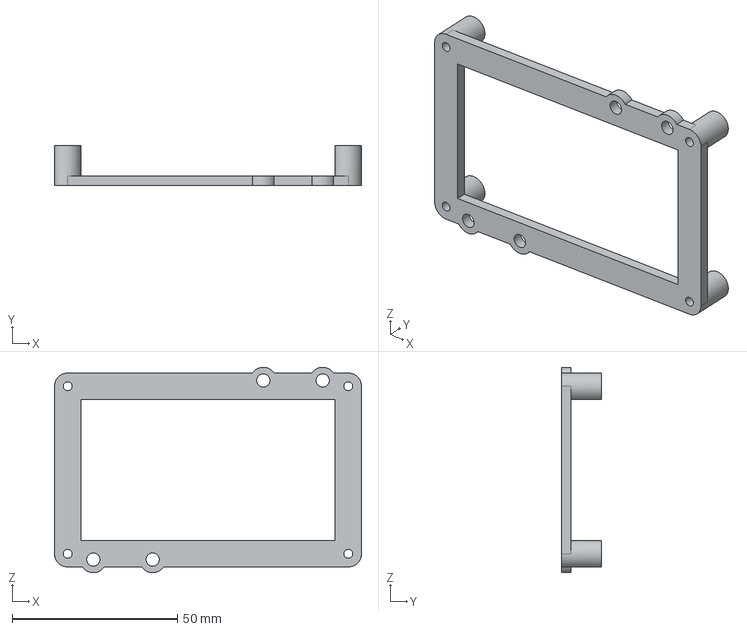
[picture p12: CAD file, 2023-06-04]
Mk5/OV5640/board_side_l_03.stp
93.0 x 12.2 x 62.2 mm

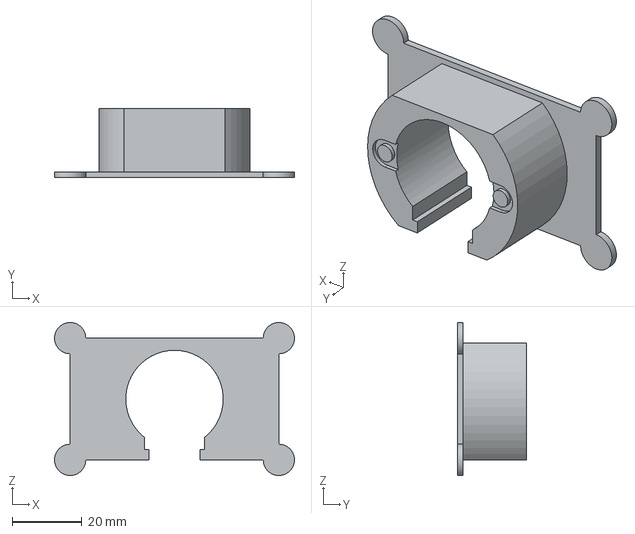
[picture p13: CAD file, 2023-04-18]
Mk5/28BYJ/Mount02.stp
69.0 x 20.0 x 44.0 mm

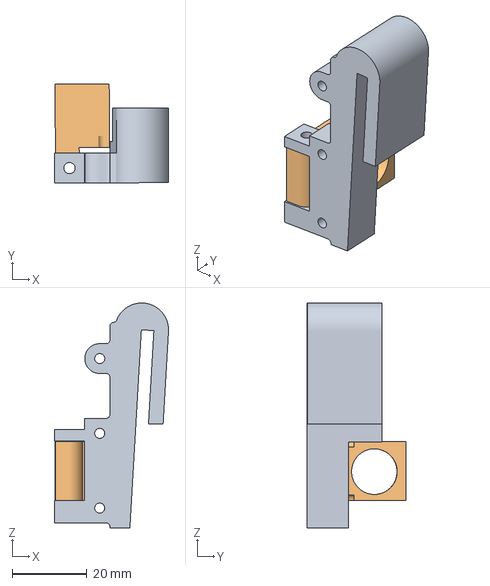
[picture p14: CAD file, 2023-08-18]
Mk5/BoxClips/hinges/lazer_holder_red_angle_05.3mf
30.5 x 26.6 x 60.2 mm
lazer_holder_red_angle_05 x 2

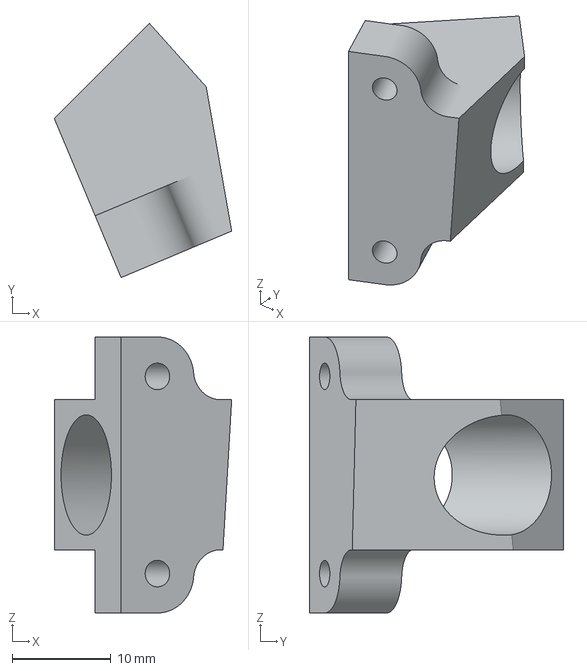
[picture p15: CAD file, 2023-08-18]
Mk5/BoxClips/lazer_holder_02a.3mf
18.0 x 25.8 x 28.0 mm

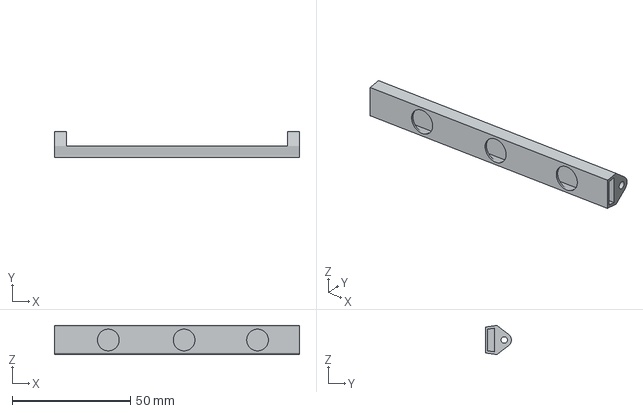
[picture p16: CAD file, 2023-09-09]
Mk5/BoxClips/lights/LED_Strip_trough_01.3mf
103.4 x 10.9 x 12.3 mm

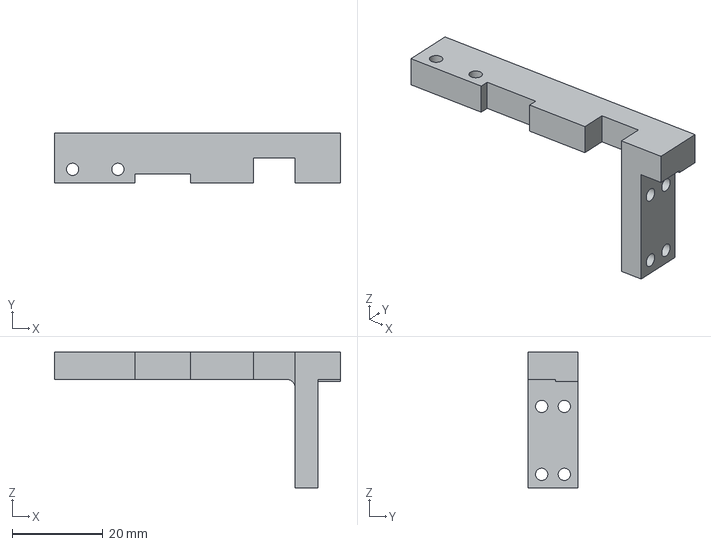
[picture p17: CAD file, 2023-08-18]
Mk5/DFRobot/MotorMountStiffener_01.3mf
63.2 x 11.0 x 30.0 mm

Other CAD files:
Mk5/DFRobot/Rotary01/Rotary04_WormGearPrint07.3mf
Mk5/gt2/180_teeth_lip_cutout_02.stp
Mk5/OV5640/board_side_l_01.stp
Mk5/28BYJ/DirectDriverTable2.stp
Mk1/experiment01/steps100_200.x_t
Mk1/experiment03/Part1.3mf
Mk1/parts/Box/MidBridgeCentralStrut01.3mf
Mk1/parts/Box/MidBridgeLower01.3mf
Mk1/parts/Box/MidBridgeLower02.3mf
Mk1/parts/Box/MidBridgeLower03.stl
Mk1/parts/Box/MotorAttachementSupports01.3mf
Mk1/parts/Box/MotorBridgeEdgeBracket1.3mf
Mk1/parts/Box/Outside_MotorAttachementSupports01.3mf
Mk1/parts/Box/ServoSupport1.3mf
Mk1/parts/Box/ServoSupportShim1.3mf
Mk1/parts/Box/TurntableStabiliser.3mf
Mk1/parts/Box/TurntableStabiliser2.3mf
Mk1/parts/Box/TurntableStabiliser2.obj
Mk1/parts/Box/pinnion_top_brace.3mf
Mk1/parts/Box/pinnion_top_brace_2.3mf
Mk1/parts/Box/pinnion_top_brace_3.3mf
Mk1/parts/Box/pinnion_top_brace_4.3mf
Mk1/parts/Calibration/StickEndPart1.3mf
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

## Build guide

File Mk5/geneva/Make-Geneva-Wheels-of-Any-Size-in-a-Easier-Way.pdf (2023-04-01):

instructables

Make Geneva Wheels of Any Size in a Easier Way (http://www.instructables.com/id/Make-Geneva-Wheels-of-Any-Size-in-a-Easier-Way/)

by iGreeny (http://www.instructables.com/member/iGreeny/)

It's not so hard to find the formulas and diagrams if you want to design a Geneva wheel of your own, and you can do it following this article: Make Geneva wheels of any size (https://newgottland.com/2012/01/08/make-geneva-wheels-of-any-size/) and this video. (https://www.youtube.com/watch?v=feA4ZfnTrSc)

but I feel it's not very friendly to non-engineer readers - at least it took me quite a while to pull out the math and geometry I've learned back in high school. So i decided to translate the formulas into plain English and clearer steps. I also made 2 videos simply recording how I designed it in Fusion 360.

Variables you can decide freely (within a reasonable range)

the quantity of the slots on the Geneva wheel; the radius of the drive pin;
the Geneva wheel radius;
drive pin clearance.

You and use any CAD software you feel comfortable with because we only need basic sketch functions for designing.

If you just want to make one without designing, goto the last step. (https://www.instructables.com/id/Make-Geneva-Wheels-of-Any-Size-in-a-Easier-Way/#step9)

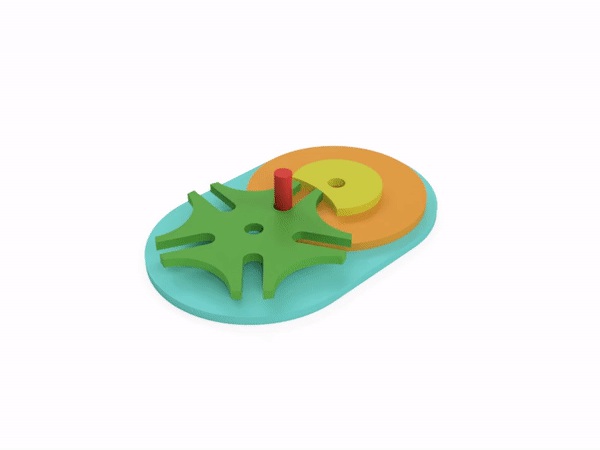
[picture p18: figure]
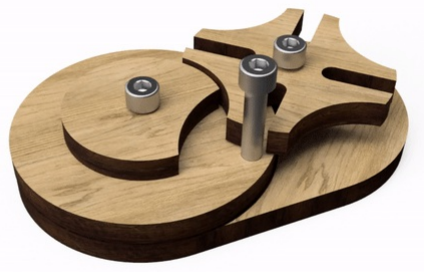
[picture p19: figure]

https://www.youtube.com/watch?v=OtfiVf5apn4&feature=youtu.be Make Geneva Wheels of Any Size in a Easier Way: Page 1

### Step 1: Start From a Triangle

A Geneva drive has 3 main components - Geneva wheel, drive wheel, and drive pin. The triangle is the linkage of the 3 parts.

I gonna design a Geneva wheel with the wheel diameter 1" and 5 slots.

You can always start with a right triangle with the right angle on the top.

the left angle =180º / the quantity of slots, for example, if I want to make 5 slots,

The angle = 180º/5 = 36º

Don't worry, this is all the math we need in this design.

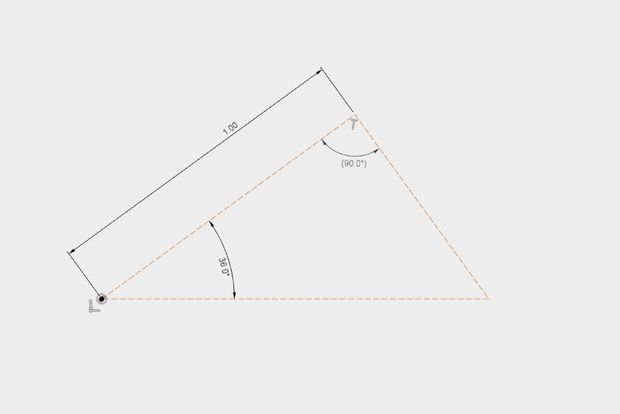
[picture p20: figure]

### Step 2: Diameters of the Geneva Wheel and the Drive Wheel

On the right triangle, draw 2 circles centered at the 2 vertexes of sharp angles that tangent to both legs.

The circle centered at the 36º angle is the diameter of the Geneva wheel, and the other is the radius of the drive pin crank.

Draw another circle centered at the vertex of the 36º angle and tangent to the right circle. The tangent point is the maximum depth (how close to the center the slots need to be) of each slot.

Make Geneva Wheels of Any Size in a Easier Way: Page 2

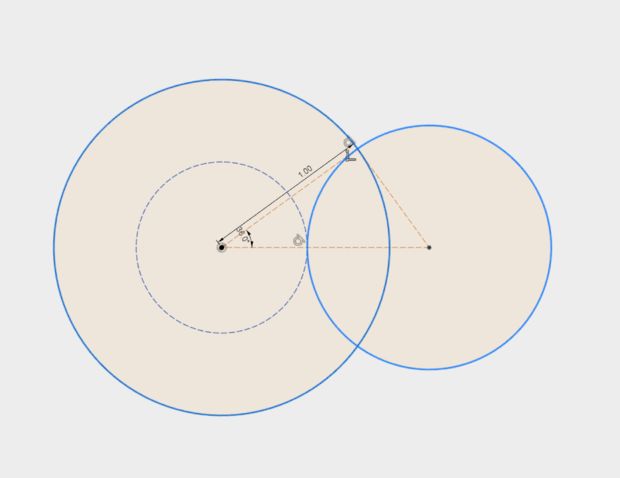
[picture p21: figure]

### Step 3: Locate the Slots and Drive Pin

Decide the drive pin dimeter.

I use 3/16" (0.1875 in") wood dowel as the drive pin, so it's safe to use 0.2" in the slots design for some clearance.

Draw 2 circles centered at both Intersections of the left leg and the left 2 circles. The one closer to the center is the end of the slot, and the farther one is the where the drive pin should be.

Draw a center to center slot.

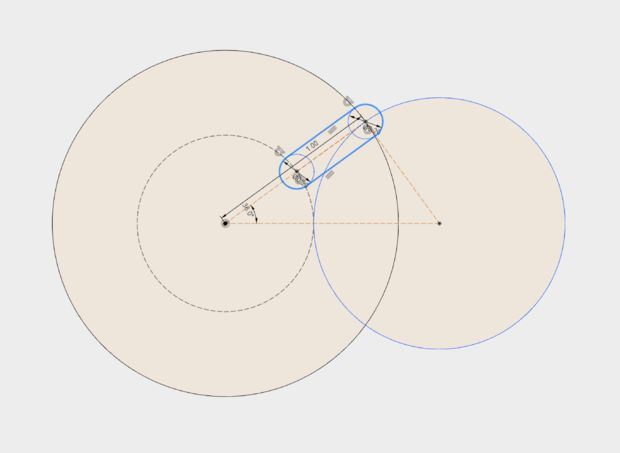
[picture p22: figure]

### Step 4: The Drive Wheel

Draw a line tangent to the left side of drive pin and perpendicular to the linkage of the 2 big circles (the cathetus of the triangle, ) then draw a circle centered at the right vertex and tangent to the line. This circle minus the intersection area with the Geneva wheel is the the drive wheel.

Use offset tool to make a little clearance to the drive wheel.

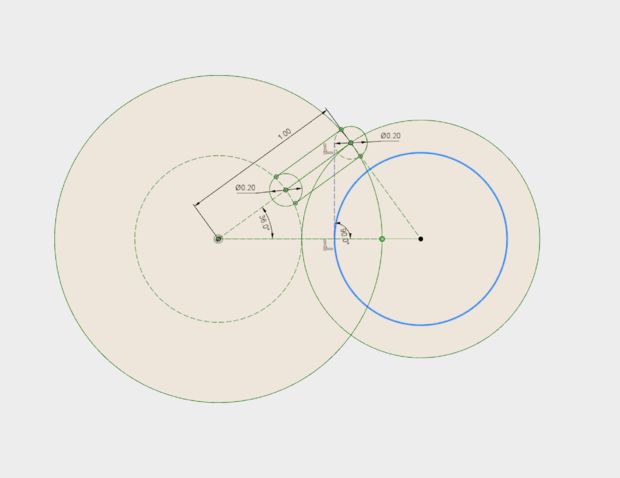
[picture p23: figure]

### Step 5: Finish the Geneva Wheel

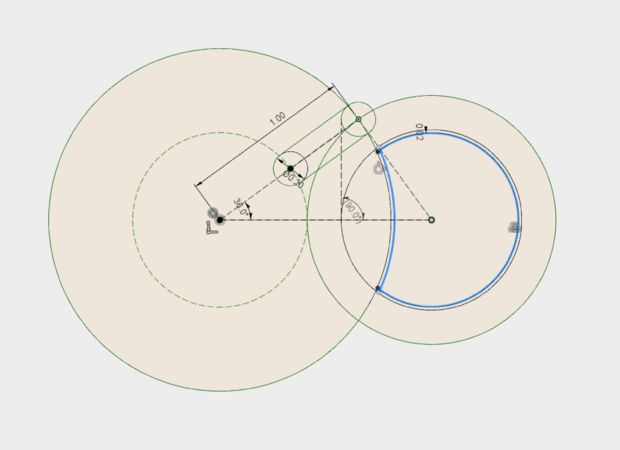
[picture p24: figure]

select the slot and the unwanted arc of the drive wheel, use circular pattern tool to copy 5 at the left vertex.

Till now all the tricky parts are done.

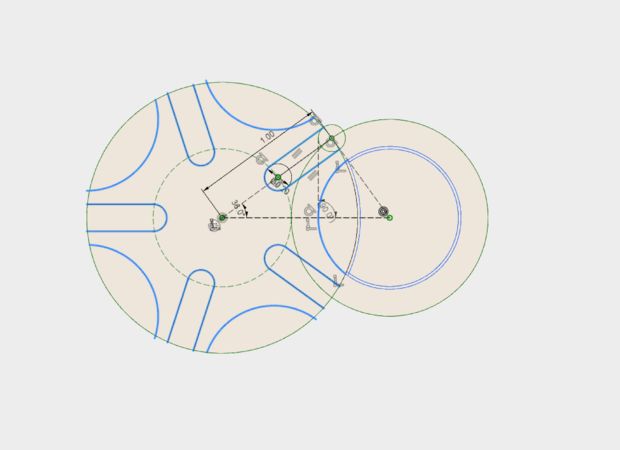
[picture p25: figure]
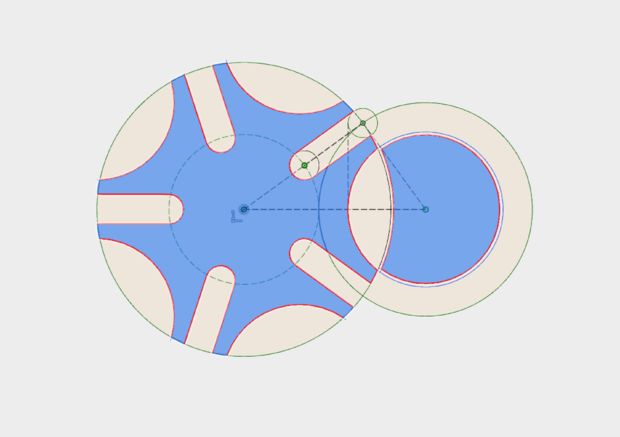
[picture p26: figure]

### Step 6: Make the Drive Crank

On the interaction of drive pin radius and cathetus, draw another circle same diameter as the drive pin.

To connect the pin the the drive wheel, you can make a bigger wheel that concentric to the drive wheel, or simply connect them with a crank. Anyway the left end of the crank shouldn't be too close to the left vertex (unless you don't want to make it in the real world.)

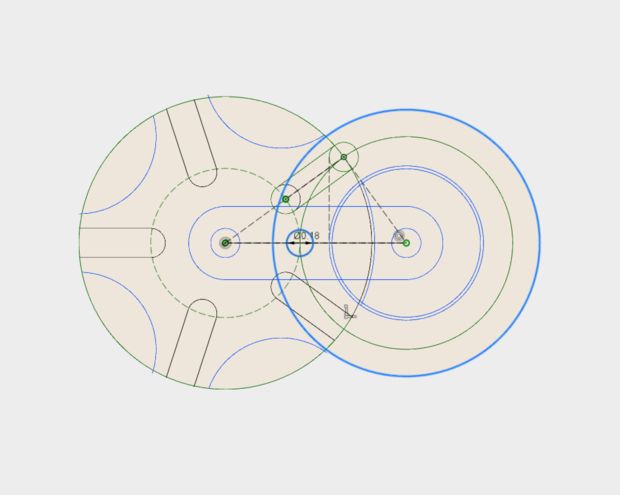
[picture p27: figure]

### Step 7: The Linkage

The linkage is used to connect the shafts of the 2 wheels.

Before drawing the linkage, you need to decide what to use as the shaft. In this design I will use 3/16 as well.

draw 2 circles at both center, this time the circles should be slightly smaller than 3/16 to hold all pieces together.

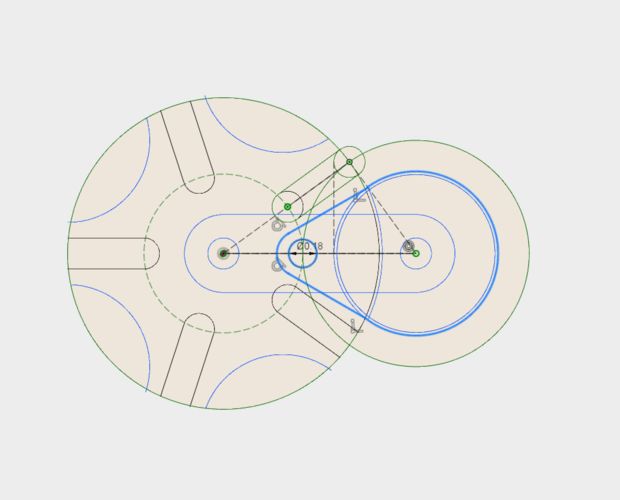
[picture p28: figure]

Draw a center to center slot as the linkage. Actually you can draw any shape as long as you have the 2 centers.

Clean up the construction lines and the design is finished.

Hope it does make things easier.

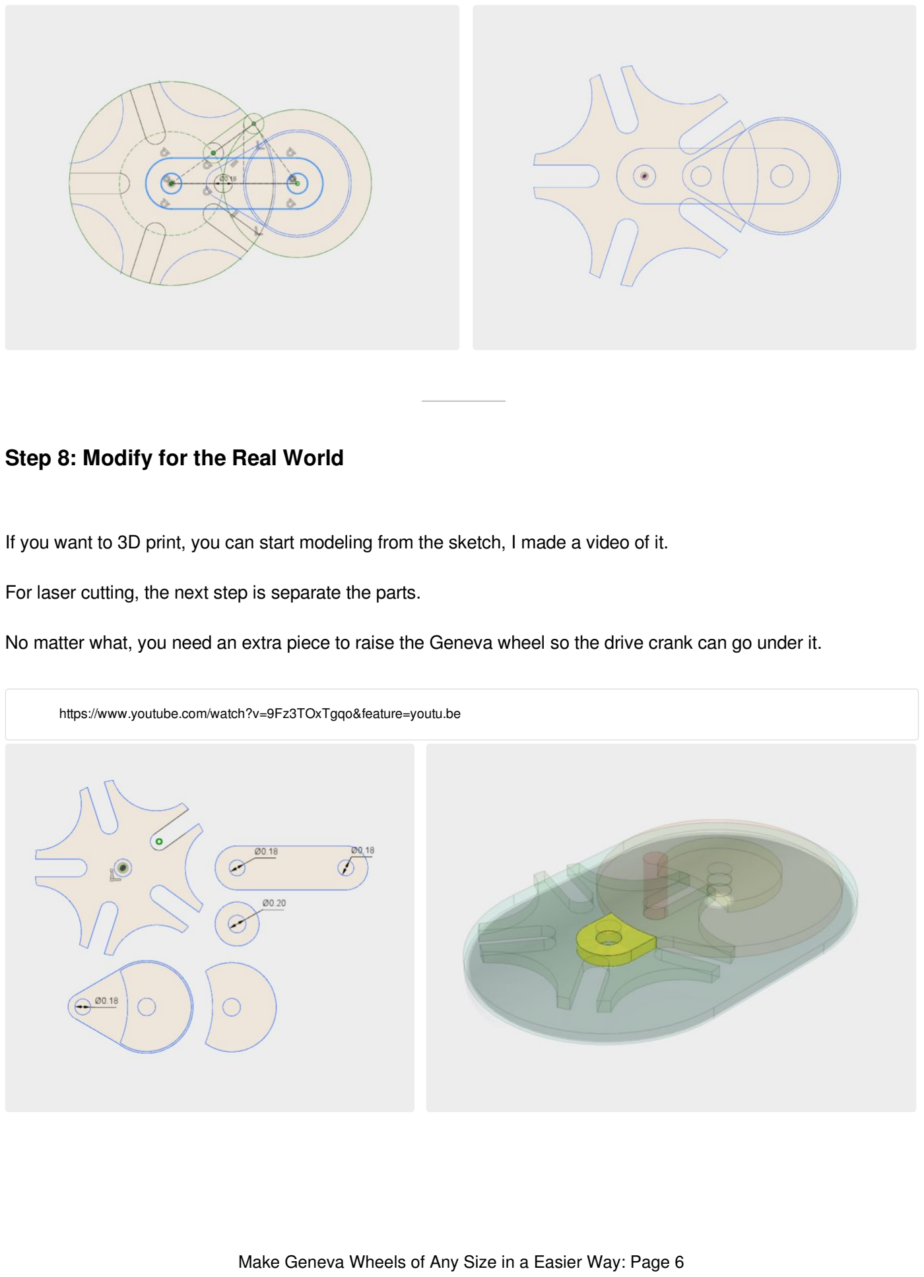
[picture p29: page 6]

### Step 8: Modify for the Real World

If you want to 3D print, you can start modeling from the sketch, I made a video of it.

For laser cutting, the next step is separate the parts.

No matter what, you need an extra piece to raise the Geneva wheel so the drive crank can go under it.

https://www.youtube.com/watch?v=9Fz3TOxTgqo&feature=youtu.be

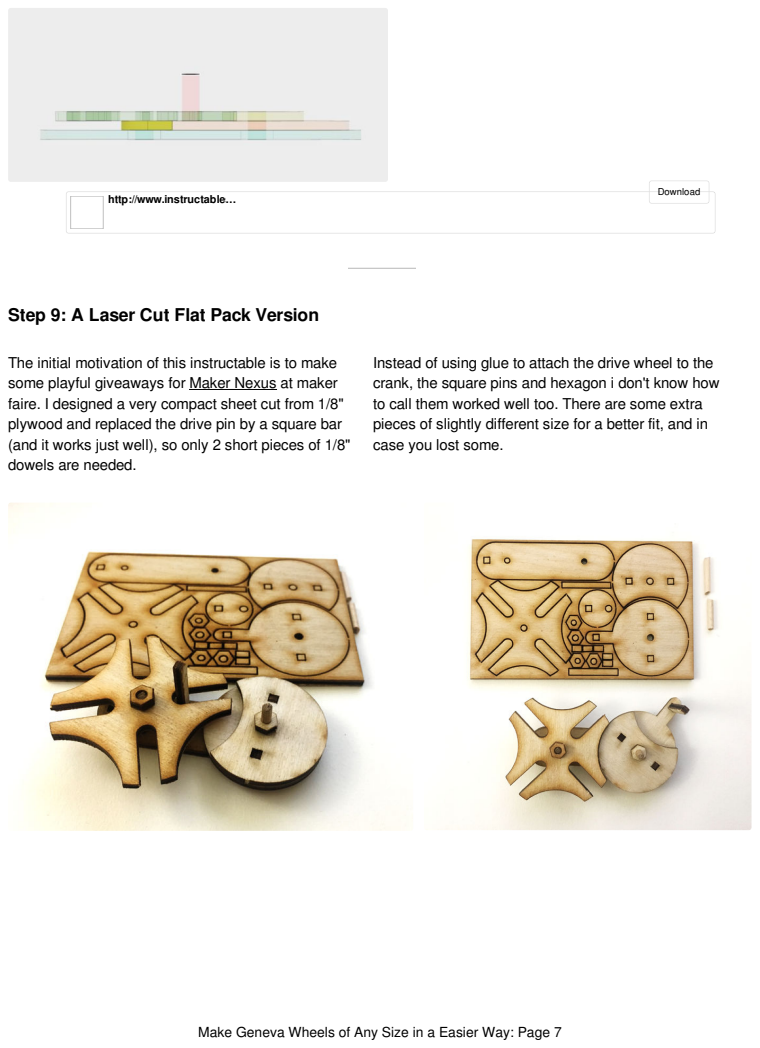
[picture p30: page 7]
Download

http://www.instructables…

Step 9: A Laser Cut Flat Pack Version

The initial motivation of this instructable is to make
some playful giveaways for Maker Nexus (https://www.makernexus.com/) at maker
faire. I designed a very compact sheet cut from 1/8"
plywood and replaced the drive pin by a square bar
(and it works just well), so only 2 short pieces of 1/8"
dowels are needed.

Instead of using glue to attach the drive wheel to the
crank, the square pins and hexagon i don't know how
to call them worked well too. There are some extra
pieces of slightly different size for a better fit, and in
case you lost some.

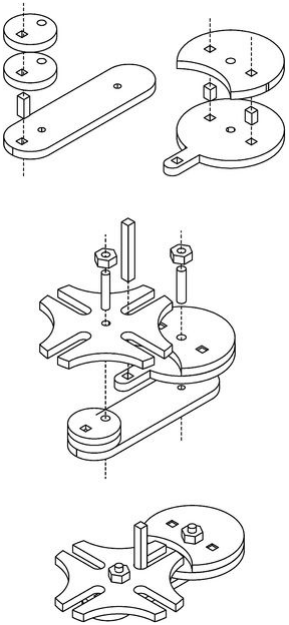
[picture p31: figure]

https://youtu.be/tju7pLETqDg

http://www.instructables…

Download (https://cdn.instructables.com/ORIG/F1M/0G94/JHIA2US0/F1M0G94JHIA2US0.svg)

This explanation is the best I've seen and I'd like to think I've looked at every option available. The timing was perfect...I need to make a Geneva wheel now for a project I'm working on. I am addicted to Sketchup and this project techniques should transfer easily. Thanks for posting it.

Can You explain what this wheel does? https://www.robives.com/blog/geneva-drive-mechanism/

Pretty nifty and actually exactly what I need

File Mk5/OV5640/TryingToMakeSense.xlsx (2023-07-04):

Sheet: Sheet1
0 |  |  |  | 0
850 | 850 |  |  | 500 | 500
1800 | 950 |  |  | 1400 | 900
2560 | 760 |  |  | 1440 | 40
 |  |  |  |  |  |  |  |  | mw | mh | sx | sy | ex | ey | ox | oy | tx | ty
 |  | X | Y |  |  |  |  | 2592 | 2560 | 1440 | 0 | 240 | 2623 | 1711 | 32 | 16 | 2844 | 1488
 | physical | 2592 | 1944 |  |  |  |  | 1944 |  |  |  |  | 2560 | 1440
 | start | 0 | 240 |  |  |  |  |  |  |  | p = m - o
 | end | 2623 | 1711 |  |  |  |  |  | 2560
 | isp input size | -31 |  |  |  |  |  |  | 2592 | 32
 |  |  |  |  |  |  |  |  | 2623 | 63
 |  |  |  |  |  |  |  |  | 2844 | 221
 |  |  |  |  |  |  |  |  | [2560, 1920, _ASPECT_RATIO_4X3], # QSXGA
 |  |  |  |  |  |  |  |  | _ASPECT_RATIO_4X3 = const(0)
 |  |  |  |  |  |  |  |  | mw | mh | sx | sy | ex | ey | ox | oy | tx | ty
 |  |  |  |  |  |  |  |  | 2560 | 1920 | 0 | 0 | 2623 | 1951 | 32 | 16 | 2844 | 1968 | # 4x3
 |  |  |  |  |  |  |  |  |  |  |  |  | 2560 | 1920
 |  |  |  | mw | 2560 |  |  |  |  |  |  |  |  |  |  | 2844 | 1968 | 4 | 3 | 4x3
 |  |  |  | mh | 1440 |  |  |  |  |  |  |  |  |  |  | 2844 | 1752 | 3 | 2 | 3x2
 |  |  |  | sx | 0 | _X_ADDR_ST_H | _X_ADDR_ST_H = const(0x3800) |  |  |  |  |  |  |  |  | 2844 | 1648 | 16 | 10 | 16x10
 |  |  |  | sy | 240 | _X_ADDR_ST_H |  |  |  |  |  |  |  |  |  | 2844 | 1584 | 5 | 3 | 5x3
 |  |  |  | ex | 2623 | _X_ADDR_END_H | _X_ADDR_END_H = const(0x3804) |  |  |  |  |  |  |  |  | 2844 | 1488 | 16 | 9 | 16x9
 |  |  |  | ey | 1711 | _X_ADDR_END_H |  |  |  |  |  |  |  |  |  | 2844 | 1128 | 21 | 9 | 21x9
 |  |  |  | ox | 16 | _X_OFFSET_H | _X_OFFSET_H = const(0x3810) |  |  | If not binning | 8 | _X_OFFSET_H |  |  |  | 2684 | 1968 | 5 | 4 | 5x4
 |  |  |  | oy | 8 | _X_OFFSET_H |  |  |  | If not binning | 4 | _X_OFFSET_H |  |  |  | 2684 | 1968 | 1 | 1 | 1x1
 |  |  |  | tx | 2644 | _X_TOTAL_SIZE_H | _X_TOTAL_SIZE_H = const(0x380C) |  |  | If not binning | 2444 | _X_TOTAL_SIZE_H |  |  |  | 1884 | 1968 | 9 | 16 | 9x16
 |  |  |  | ty | 744 | _X_TOTAL_SIZE_H |  |  |  | If not binning | 372 | _X_TOTAL_SIZE_H
 |  |  |  | scale | 0 | _ISP_CONTROL_01 | _ISP_CONTROL_01 = const(0x5001) |  |  | 0x20
 |  |  |  |  | 0x380C | TIMING HTS | 0x0B | 0B1C | 2844
 |  |  |  |  | 0x380D | TIMING HTS | 0x1C
 |  |  |  |  | 2560
 |  |  |  |  | 1440
 |  |  |  |  | 24.00 | 3686400 | Pixels
 |  |  |  |  |  | 153600.00 | bytes
 |  |  |  |  |  | 150.00 | kb |  |  |  | 900 | 900 | 2 | 1620000
 |  |  |  |  |  |  | 76800 | available pixels |  |  | self.width * self.height // self.quality
 |  |  |  |  |  |  |  | -76800.00 |  |  | 960 | 960 | 6 | 153600
 |  |  |  |  |  |  |  | I want the middle third of the screen |  |  | 960 | 960 | 5 | 184320
 |  |  |  |  |  |  | 37.109375% | 65.97222222%
 |  |  |  |  |  |  | 900 | 900
 |  |  |  |  |  |  | 270 | 270 | 72900
 |  |  |  |  |  |  | 850 | 950 | 1800
 |  |  |  |  | width | 950 | 285 | 285
 |  |  |  |  | height | 900 | 270
 |  |  |  |  |  | 19 | 76950 | -150
 |  |  |  |  |  | 18.00
 |  |  |  |  |  | 1920 | 2560 | 1920 | 4x3
 |  |  |  |  |  | 1706.666667 | 2560 | 1704 | 3x2
 |  |  |  |  |  |  | 2560 | 1600 | 16x10
 |  |  |  |  |  |  | 2560 | 1536 | 5x3
 |  |  |  |  |  |  | 2560 | 1440 | 16x9
 |  |  |  |  |  |  | 2560 | 1080 | 21x9
 |  |  |  |  |  |  | 2400 | 1920 | 5x4
 |  |  |  |  |  |  | 1920 | 1920 | 1x1
 |  |  |  |  |  |  | 1088 | 1920 | 9x16
 |  |  |  |  |  |  | 1820 | 1920 | 18x19
 |  |  |  |  |  |  | 950 | 900 | 19x18
 |  |  |  |  |  |  | 2650 | 1820 | 19x18
2060 | #NUM! |  |  |  | 1536 |  |  | 1584 |  | 48
984 | #NUM! |  |  | 2560 | 1440 |  | 2844 | 1488 | 284 | 48
 |  |  |  | 2560 | 1080 |  | 2844 | 1128 | 284 | 48
 |  |  |  |  | 1820 |  |  | 1868
0B | 1011
1C | 11100
 |  |  | 2560 | 1920 | 320 | 2543 | 31 | 2684
 |  |  | 1440 | 1920 | 0 | 1951 | 16 | 1968
 |  |  |  |  |  |  | 960 | 1920
 |  |  |  |  |  |  |  | 2952
 |  |  | 2592 | 2684 | 92
 |  |  | 1944 | 1968 | 24 | 12

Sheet: Sheet2
Name | Default | Comment | Property?
self._bank | Seems to only be set to None | Seems to only be set to None | N/A
self._binning | FALSE | Changed within _set_size_and_colorspace() | N/A
self._colorspace | OV5640_COLOR_RGB | Enum - defaults to RGB | colorspace
self._effect | OV5640_SPECIAL_EFFECT_ | Enum for special effects | effect
self._ev | 0 | Sensor exposure (-4 to 4) | exposure_value
self._flip_x | FALSE | - | flip_x
self._flip_y | FALSE | - | flip_y
self._h | NONE | In _set_size_and_colorspace() this is set from values within _resolution_info[] table | height
self._saturation | 0 | self._write_register(0x5381 + offset, reg_value) | saturation
self._scale | FALSE | Set and used within _set_size_and_colorspace() | N/A
self._set_colorspace() | Method | Use ._colorspace to lookup into _ov5640_color_settings[] table | N/A
self._set_image_options() | Method | Uses loads of flip/binning/colourspace values to set registers - doesn't call other methods | N/A
self._set_pll | Method | This sets a lot of hardcode registers | N/A
self._set_size_and_colorspace() | Method | This is the business. I think some of the setters here trigger other methods | N/A
self._size | OV5640_SIZE_QQVGA, | Setter calls self._set_size_and_colorspace() | size
self._test_pattern | FALSE | - | test_pattern
self._w | NONE | In _set_size_and_colorspace() this is set from values within _resolution_info[] table | width
self._white_balance | 0 | Defaults to Auto | white_balance
self._i2c_device | N/A | N/A
self._imagecapture | N/A | N/A
self._imagecapture.capture() | N/A | N/A
self._imagecapture.deinit() | N/A | N/A
self._mclk_pwm | N/A | # Initialize the master clock
self._mclk_pwm.deinit() | N/A | N/A
self._mclk_pwm.duty_cycle | N/A | N/A
self._mclk_pwm.frequency self._mclk_pwm else None |  | The frequency of the master clock to generate | mclk_frequency
self._reset | N/A | N/A
self._reset.deinit() | N/A | N/A
self._reset.switch_to_output | N/A | N/A
self._shutdown | N/A | N/A
self._shutdown.deinit() | N/A | N/A
self._shutdown.switch_to_output(False) | N/A | N/A
self._shutdown: | N/A | N/A

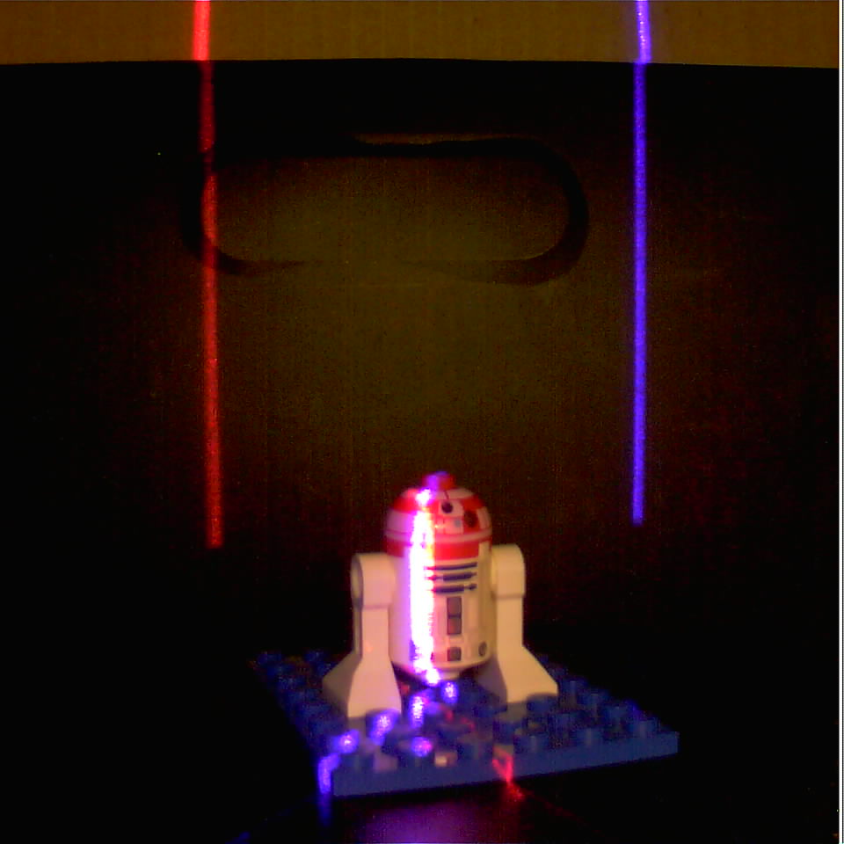
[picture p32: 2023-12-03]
Mk5/Code/20_100StepTurnsTakingPictures/run_037/capture_063_960x960_6.jpg

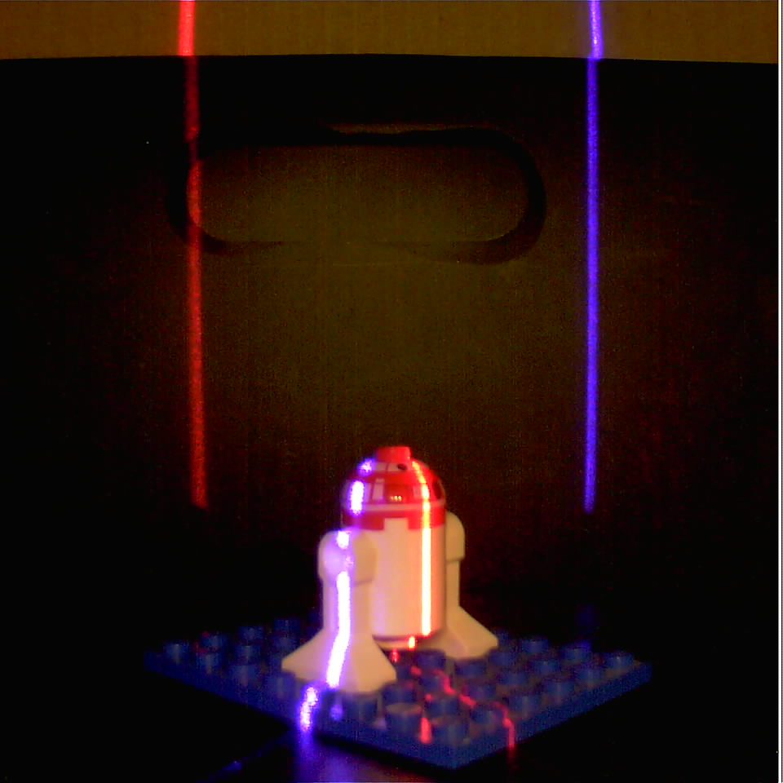
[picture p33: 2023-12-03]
Mk5/Code/20_100StepTurnsTakingPictures/run_037/capture_020_960x960_6.jpg

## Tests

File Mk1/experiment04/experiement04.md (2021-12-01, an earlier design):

#2021.10.31#

I've mounted a tape measure to the top of the turn table, now I need code that doesn't try to turn the turntable and wreck the gears!

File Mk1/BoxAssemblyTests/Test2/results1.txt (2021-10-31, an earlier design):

FullyRetractPoker
Table Homing
Moving table to upper limit
Moving table to upper limit - done
Table retract from upper limit
Table retract from upper limit - done
Table seek upper limit
Table seek upper limit - done
Table Homed
Poker Homing
FullyRetractPoker
Fully retract and confirm sensor reset - done
MovePokerToNearTableEdge
Stage Poker and confirm sensor available - done
FullyRetractPoker
Fully retract poker ready for table movement - done
Poker Homed
ConfirmFirstMeasureToSideOfTable()
FullyRetractPoker
MovePokerToNearTableEdge
Measuring - starting
FullyRetractPoker
Table measured at :134
ConfirmFirstMeasureToSideOfTable() - done
MoveTableToScanStartPosition()
Done!
Traceback (most recent call last):
  File "code.py", line 465, in <module>
KeyboardInterrupt: 

Code done running.
Auto-reload is on. Simply save files over USB to run them or enter REPL to disable.

Press any key to enter the REPL. Use CTRL-D to reload.

Adafruit CircuitPython 6.3.0 on 2021-06-01; Raspberry Pi Pico with rp2040
>>> [D
... Traceback (most recent call last):
  File "<stdin>", line 2
SyntaxError: invalid syntax
>>> 
soft reboot

Auto-reload is on. Simply save files over USB to run them or enter REPL to disable.

code.py output:

Code stopped by auto-reload.
soft reboot

Auto-reload is on. Simply save files over USB to run them or enter REPL to disable.

code.py output:
FullyRetractPoker
Table Homing
Moving table to upper limit
Moving table to upper limit - done
Table retract from upper limit
Table retract from upper limit - done
Table seek upper limit
Table seek upper limit - done
Table Homed
Poker Homing
FullyRetractPoker
Fully retract and confirm sensor reset - done
MovePokerToNearTableEdge
Stage Poker and confirm sensor available - done
FullyRetractPoker
Fully retract poker ready for table movement - done
Poker Homed
ConfirmFirstMeasureToSideOfTable()
FullyRetractPoker
MovePokerToNearTableEdge
Measuring - starting
FullyRetractPoker
Table measured at :134
ConfirmFirstMeasureToSideOfTable() - done
MoveTableToScanStartPosition()
MoveTableToScanStartPosition() - done
Press confirm to begin scan?
PerformScan
Revolution 0
Lower limit reached
PANIC
OK button releases panic
PerformScan
Revolution 0
Lower limit reached
PANIC
OK button releases panic
PerformScan
Revolution 0
Lower limit reached
PANIC
OK button releases panic
PerformScan
Revolution 0
Lower limit reached
PANIC
OK button releases panic
PerformScan
Revolution 0
Lower limit reached
PANIC
OK button releases panic
PerformScan
Revolution 0
Lower limit reached
PANIC
OK button releases panic
PerformScan
Revolution 0
Lower limit reached
PANIC
OK button releases panic
PerformScan
Revolution 0
Lower limit reached
PANIC
OK button releases panic
PerformScan
Revolution 0
Lower limit reached
PANIC
OK button releases panic
PerformScan
Revolution 0
Lower limit reached
PANIC
OK button releases panic
PerformScan
Revolution 0
Lower limit reached
PANIC
OK button releases panic
PerformScan
Revolution 0
Lower limit reached
PANIC
OK button releases panic
PerformScan
Revolution 0
Lower limit reached
PANIC
OK button releases panic
PerformScan
Revolution 0
Lower limit reached
PANIC
OK button releases panic

Code stopped by auto-reload.
soft reboot

Auto-reload is on. Simply save files over USB to run them or enter REPL to disable.

code.py output:
Lower limit switch is pressed
Lower limit switch is pressed
Lower limit switch is pressed
Lower limit switch is pressed
Lower limit switch is pressed
Lower limit switch is pressed
Lower limit switch is pressed

Code stopped by auto-reload.
soft reboot

Auto-reload is on. Simply save files over USB to run them or enter REPL to disable.

code.py output:
FullyRetractPoker
Table Homing
Moving table to upper limit
Moving table to upper limit - done
Table retract from upper limit
Table retract from upper limit - done
Table seek upper limit
Table seek upper limit - done
Table Homed
Poker Homing
FullyRetractPoker
Fully retract and confirm sensor reset - done
MovePokerToNearTableEdge
Stage Poker and confirm sensor available - done
FullyRetractPoker
Fully retract poker ready for table movement - done
Poker Homed
ConfirmFirstMeasureToSideOfTable()
FullyRetractPoker
MovePokerToNearTableEdge
Measuring - starting
FullyRetractPoker
Table measured at :134
ConfirmFirstMeasureToSideOfTable() - done
MoveTableToScanStartPosition()
Done!

Code stopped by auto-reload.
soft reboot

Auto-reload is on. Simply save files over USB to run them or enter REPL to disable.

code.py output:

Code stopped by auto-reload.
soft reboot

Auto-reload is on. Simply save files over USB to run them or enter REPL to disable.

code.py output:
FullyRetractPoker
Table Homing
Moving table to upper limit
Moving table to upper limit - done
Table retract from upper limit
Table retract from upper limit - done
Table seek upper limit
Table seek upper limit - done
Table Homed
Poker Homing
FullyRetractPoker
Fully retract and confirm sensor reset - done
MovePokerToNearTableEdge
Stage Poker and confirm sensor available - done
FullyRetractPoker
Fully retract poker ready for table movement - done
Poker Homed
ConfirmFirstMeasureToSideOfTable()
FullyRetractPoker
MovePokerToNearTableEdge
Measuring - starting
FullyRetractPoker
Table measured at :134
ConfirmFirstMeasureToSideOfTable() - done
MoveTableToScanStartPosition()
MoveTableToScanStartPosition() - done
Press confirm to begin scan?
PerformScan
Revolution 0
FullyRetractPoker
MovePokerToNearTableEdge
Measuring - starting
FullyRetractPoker
0:0 touched True angle 118
FullyRetractPoker
MovePokerToNearTableEdge
Measuring - starting
FullyRetractPoker
0:1 touched True angle 117
FullyRetractPoker
MovePokerToNearTableEdge
Measuring - starting
FullyRetractPoker
0:2 touched True angle 117
FullyRetractPoker
MovePokerToNearTableEdge
Measuring - starting
PANIC
Traceback (most recent call last):
  File "code.py", line 463, in <module>
  File "code.py", line 445, in PrepareThenPerformScan
  File "code.py", line 370, in PerformScan
  File "code.py", line 343, in MakeOneFullRevolvePrintingAngles
  File "code.py", line 328, in StepNextChunkAndTakeMeasurement
  File "code.py", line 249, in TakeMeasurement
  File "code.py", line 100, in MoveServo
  File "code.py", line 88, in CheckEBreak
  File "code.py", line 81, in Panic
KeyboardInterrupt: 

Code done running.

Press any key to enter the REPL. Use CTRL-D to reload.

Adafruit CircuitPython 6.3.0 on 2021-06-01; Raspberry Pi Pico with rp2040
>>> 
soft reboot

Auto-reload is on. Simply save files over USB to run them or enter REPL to disable.

code.py output:
Table Homing
Moving table to upper limit
Moving table to upper limit - done
Table retract from upper limit
Table retract from upper limit - done
Table seek upper limit
Table seek upper limit - done
Table Homed
Poker Homing
Fully retract and confirm sensor reset - done
Stage Poker and confirm sensor available - done
Fully retract poker ready for table movement - done
Poker Homed
ConfirmFirstMeasureToSideOfTable()
Table measured at :134
ConfirmFirstMeasureToSideOfTable() - done
MoveTableToScanStartPosition()
MoveTableToScanStartPosition() - done
Press confirm to begin scan?
PerformScan
Revolution 0
0:0 touched True angle 118
0:1 touched True angle 117
0:2 touched True angle 117
0:3 touched True angle 117
0:4 touched True angle 117
0:5 touched True angle 116
0:6 touched True angle 116
0:7 touched True angle 116
0:8 touched True angle 116
0:9 touched True angle 115
0:10 touched True angle 115
0:11 touched True angle 114
0:12 touched True angle 114
0:13 touched True angle 114
0:14 touched True angle 114
0:15 touched True angle 113
0:16 touched True angle 113
0:17 touched True angle 113
0:18 touched True angle 112
0:19 touched True angle 112
0:20 touched True angle 111
0:21 touched True angle 111
0:22 touched True angle 111
0:23 touched True angle 111
0:24 touched True angle 110
0:25 touched True angle 110
0:26 touched True angle 110
0:27 touched True angle 110
0:28 touched True angle 130
0:29 touched True angle 130
0:30 touched True angle 129
0:31 touched True angle 128
0:32 touched True angle 128
0:33 touched True angle 127
0:34 touched True angle 127
0:35 touched True angle 126
0:36 touched True angle 126
0:37 touched True angle 125
0:38 touched True angle 124
0:39 touched True angle 124
0:40 touched True angle 124
0:41 touched True angle 123
0:42 touched True angle 123
0:43 touched True angle 122
0:44 touched True angle 121
0:45 touched True angle 121
0:46 touched True angle 120
0:47 touched True angle 120
0:48 touched True angle 119
0:49 touched True angle 119
0:50 touched True angle 118
Revolution 1
1:0 touched True angle 118
1:1 touched True angle 118
1:2 touched True angle 118
1:3 touched True angle 117
1:4 touched True angle 117
1:5 touched True angle 116
1:6 touched True angle 116
1:7 touched True angle 116
1:8 touched True angle 116
1:9 touched True angle 115
1:10 touched True angle 115
1:11 touched True angle 115
1:12 touched True angle 114
1:13 touched True angle 114
1:14 touched True angle 114
1:15 touched True angle 113
1:16 touched True angle 113
1:17 touched True angle 113
1:18 touched True angle 113
1:19 touched True angle 112
1:20 touched True angle 112
1:21 touched True angle 112
1:22 touched True angle 111
1:23 touched True angle 111
1:24 touched True angle 111
1:25 touched True angle 111
1:26 touched True angle 110
1:27 touched True angle 110
1:28 touched True angle 130
1:29 touched True angle 130
1:30 touched True angle 129
1:31 touched True angle 129
1:32 touched True angle 128
1:33 touched True angle 128
1:34 touched True angle 127
1:35 touched True angle 127
1:36 touched True angle 126
1:37 touched True angle 125
1:38 touched True angle 125
1:39 touched True angle 124
1:40 touched True angle 124
1:41 touched True angle 124
1:42 touched True angle 123
1:43 touched True angle 123
1:44 touched True angle 122
1:45 touched True angle 121
1:46 touched True angle 121
1:47 touched True angle 120
1:48 touched True angle 119
1:49 touched True angle 119
1:50 touched True angle 119
Revolution 2
2:0 touched True angle 118
2:1 touched True angle 118
2:2 touched True angle 118
2:3 touched True angle 117
2:4 touched True angle 118
2:5 touched True angle 117
2:6 touched True angle 117
2:7 touched True angle 116
2:8 touched True angle 116
2:9 touched True angle 116
2:10 touched True angle 116
2:11 touched True angle 115
2:12 touched True angle 115
2:13 touched True angle 114
2:14 touched True angle 114
2:15 touched True angle 114
2:16 touched True angle 114
2:17 touched True angle 113
2:18 touched True angle 113
2:19 touched True angle 113
2:20 touched True angle 112
2:21 touched True angle 112
2:22 touched True angle 111
2:23 touched True angle 111
2:24 touched True angle 111
2:25 touched True angle 111
2:26 touched True angle 110
2:27 touched True angle 110
2:28 touched True angle 131
2:29 touched True angle 130
2:30 touched True angle 130
2:31 touched True angle 129
2:32 touched True angle 129
2:33 touched True angle 128
2:34 touched True angle 127
2:35 touched True angle 127
2:36 touched True angle 126
2:37 touched True angle 126
2:38 touched True angle 125
2:39 touched True angle 125
2:40 touched True angle 124
2:41 touched True angle 124
2:42 touched True angle 124
2:43 touched True angle 123
2:44 touched True angle 122
2:45 touched True angle 121
2:46 touched True angle 121
2:47 touched True angle 120
2:48 touched True angle 120
2:49 touched True angle 119
2:50 touched True angle 119
Revolution 3
3:0 touched True angle 119
3:1 touched True angle 118
3:2 touched True angle 118
3:3 touched True angle 118
3:4 touched True angle 118
3:5 touched True angle 117
3:6 touched True angle 117
3:7 touched True angle 116
3:8 touched True angle 116
3:9 touched True angle 116
3:10 touched True angle 116
3:11 touched True angle 115
3:12 touched True angle 115
3:13 touched True angle 115
3:14 touched True angle 115
3:15 touched True angle 114
3:16 touched True angle 114
3:17 touched True angle 113
3:18 touched True angle 113
3:19 touched True angle 113
3:20 touched True angle 112
3:21 touched True angle 112
3:22 touched True angle 112
3:23 touched True angle 111
3:24 touched True angle 111
3:25 touched True angle 111
3:26 touched True angle 111
3:27 touched True angle 111
3:28 touched True angle 131
3:29 touched True angle 130
3:30 touched True angle 130
3:31 touched True angle 129
3:32 touched True angle 129
3:33 touched True angle 128
3:34 touched True angle 128
3:35 touched True angle 127
3:36 touched True angle 126
3:37 touched True angle 126
3:38 touched True angle 125
3:39 touched True angle 125
3:40 touched True angle 125
3:41 touched True angle 124
3:42 touched True angle 124
3:43 touched True angle 123
3:44 touched True angle 122
3:45 touched True angle 121
3:46 touched True angle 121
3:47 touched True angle 120
3:48 touched True angle 120
3:49 touched True angle 120
3:50 touched True angle 119
Revolution 4
4:0 touched True angle 119
4:1 touched True angle 118
4:2 touched True angle 118
4:3 touched True angle 118
4:4 touched True angle 118
4:5 touched True angle 117
4:6 touched True angle 117
4:7 touched True angle 117
4:8 touched True angle 117
4:9 touched True angle 116
4:10 touched True angle 116
4:11 touched True angle 115
4:12 touched True angle 115
4:13 touched True angle 115
4:14 touched True angle 115
4:15 touched True angle 114
4:16 touched True angle 114
4:17 touched True angle 114
4:18 touched True angle 113
4:19 touched True angle 113
4:20 touched True angle 112
4:21 touched True angle 112
4:22 touched True angle 112
4:23 touched True angle 112
4:24 touched True angle 111
4:25 touched True angle 111
4:26 touched True angle 111
4:27 touched True angle 111
4:28 touched True angle 131
4:29 touched True angle 130
4:30 touched True angle 130
4:31 touched True angle 129
4:32 touched True angle 129
4:33 touched True angle 128
4:34 touched True angle 128
4:35 touched True angle 127
4:36 touched True angle 127
4:37 touched True angle 126
4:38 touched True angle 125
4:39 touched True angle 125
4:40 touched True angle 125
4:41 touched True angle 124
4:42 touched True angle 124
4:43 touched True angle 123
4:44 touched True angle 123
4:45 touched True angle 122
4:46 touched True angle 121
4:47 touched True angle 120
4:48 touched True angle 120
4:49 touched True angle 120
4:50 touched True angle 119
PerformScan - done

Clipped:
0	0 	118
0	1 	117
0	2 	117
0	3 	117
0	4 	117
0	5 	116
0	6 	116
0	7 	116
0	8 	116
0	9 	115
0	10 	115
0	11 	114
0	12 	114
0	13 	114
0	14 	114
0	15 	113
0	16 	113
0	17 	113
0	18 	112
0	19 	112
0	20 	111
0	21 	111
0	22 	111
0	23 	111
0	24 	110
0	25 	110
0	26 	110
0	27 	110
0	28 	130
0	29 	130
0	30 	129
0	31 	128
0	32 	128
0	33 	127
0	34 	127
0	35 	126
0	36 	126
0	37 	125
0	38 	124
0	39 	124
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

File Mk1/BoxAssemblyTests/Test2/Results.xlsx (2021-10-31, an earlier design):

Revolution | Step | Angle |  | 0 | 1 | 2 | 3 | 4 | Average | 0 | 1 | 2 | 3 | 4 | Average | MM
0 | 0 | 118 | 0 | 118 | 118 | 118 | 119 | 119 | 118.4 | 130 | 130 | 131 | 131 | 131 | 130.6 | 55.1
0 | 1 | 117 | 1 | 117 | 118 | 118 | 118 | 118 | 117.8 | 130 | 130 | 130 | 130 | 130 | 130 | 54.1 |  | 130 = 54.1mm
0 | 2 | 117 | 2 | 117 | 118 | 118 | 118 | 118 | 117.8 | 129 | 129 | 130 | 130 | 130 | 129.6 | 53.1 |  | 129.6 = 53.1mm
0 | 3 | 117 | 3 | 117 | 117 | 117 | 118 | 118 | 117.4 | 128 | 129 | 129 | 129 | 129 | 128.8 | 52.1 |  | 128.8 = 52.1mm
0 | 4 | 117 | 4 | 117 | 117 | 118 | 118 | 118 | 117.6 | 128 | 128 | 129 | 129 | 129 | 128.6 | 51.1 |  | 128.6 = 51.1mm
0 | 5 | 116 | 5 | 116 | 116 | 117 | 117 | 117 | 116.6 | 127 | 128 | 128 | 128 | 128 | 127.8 | 50.1 |  | 127.8 = 50.1mm
0 | 6 | 116 | 6 | 116 | 116 | 117 | 117 | 117 | 116.6 | 127 | 127 | 127 | 128 | 128 | 127.4 | 49.1 |  | 127.4 = 49.1mm
0 | 7 | 116 | 7 | 116 | 116 | 116 | 116 | 117 | 116.2 | 126 | 127 | 127 | 127 | 127 | 126.8 | 48.1 |  | 126.8 = 48.1mm
0 | 8 | 116 | 8 | 116 | 116 | 116 | 116 | 117 | 116.2 | 126 | 126 | 126 | 126 | 127 | 126.2 | 47.1 |  | 126.2 = 47.1mm
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

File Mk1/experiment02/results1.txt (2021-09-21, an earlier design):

start experiment
Step:	 0 	Range:	 61
Step:	 1 	Range:	 63
Step:	 2 	Range:	 61
Step:	 3 	Range:	 64
Step:	 4 	Range:	 65
Step:	 5 	Range:	 67
Step:	 6 	Range:	 69
Step:	 7 	Range:	 72
Step:	 8 	Range:	 76
Step:	 9 	Range:	 71
Step:	 10 	Range:	 69
Step:	 11 	Range:	 71
Step:	 12 	Range:	 78
Step:	 13 	Range:	 79
Step:	 14 	Range:	 255
Step:	 15 	Range:	 255
Step:	 16 	Range:	 255
Step:	 17 	Range:	 255
Step:	 18 	Range:	 255
Step:	 19 	Range:	 255
Step:	 20 	Range:	 255
Step:	 21 	Range:	 255
Step:	 22 	Range:	 255
Step:	 23 	Range:	 255
Step:	 24 	Range:	 105
Step:	 25 	Range:	 109
Step:	 26 	Range:	 112
Step:	 27 	Range:	 118
Step:	 28 	Range:	 123
Step:	 29 	Range:	 126
Step:	 30 	Range:	 137
Step:	 31 	Range:	 141
Step:	 32 	Range:	 141
Step:	 33 	Range:	 143
Step:	 34 	Range:	 149
Step:	 35 	Range:	 152
Step:	 36 	Range:	 152
Step:	 37 	Range:	 158
Step:	 38 	Range:	 158
Step:	 39 	Range:	 163
Step:	 40 	Range:	 159
Step:	 41 	Range:	 162
Step:	 42 	Range:	 164
Step:	 43 	Range:	 162
Step:	 44 	Range:	 163
Step:	 45 	Range:	 162
Step:	 46 	Range:	 156
Step:	 47 	Range:	 158
Step:	 48 	Range:	 157
Step:	 49 	Range:	 159
Step:	 50 	Range:	 149
Step:	 51 	Range:	 138
Step:	 52 	Range:	 99
Step:	 53 	Range:	 73
Step:	 54 	Range:	 90
Step:	 55 	Range:	 97
Step:	 56 	Range:	 96
Step:	 57 	Range:	 99
Step:	 58 	Range:	 96
Step:	 59 	Range:	 90
Step:	 60 	Range:	 87
Step:	 61 	Range:	 80
Step:	 62 	Range:	 79
Step:	 63 	Range:	 75
Step:	 64 	Range:	 69
Step:	 65 	Range:	 65
Step:	 66 	Range:	 61
Step:	 67 	Range:	 62
Step:	 68 	Range:	 67
Step:	 69 	Range:	 64
Step:	 70 	Range:	 63
Step:	 71 	Range:	 59
Step:	 72 	Range:	 59
Step:	 73 	Range:	 56
Step:	 74 	Range:	 59
Step:	 75 	Range:	 58
Step:	 76 	Range:	 57
Step:	 77 	Range:	 57
Step:	 78 	Range:	 53
Step:	 79 	Range:	 50
Step:	 80 	Range:	 57
Step:	 81 	Range:	 58
Step:	 82 	Range:	 56
Step:	 83 	Range:	 58
Step:	 84 	Range:	 48
Step:	 85 	Range:	 59
Step:	 86 	Range:	 57
Step:	 87 	Range:	 57
Step:	 88 	Range:	 55
Step:	 89 	Range:	 50
Step:	 90 	Range:	 50
Step:	 91 	Range:	 57
Step:	 92 	Range:	 51
Step:	 93 	Range:	 56
Step:	 94 	Range:	 53
Step:	 95 	Range:	 52
Step:	 96 	Range:	 55
Step:	 97 	Range:	 53
Step:	 98 	Range:	 44
Step:	 99 	Range:	 42
Step:	 100 	Range:	 39
Step:	 101 	Range:	 34
Step:	 102 	Range:	 39
Step:	 103 	Range:	 41
Step:	 104 	Range:	 40
Step:	 105 	Range:	 47
Step:	 106 	Range:	 55
Step:	 107 	Range:	 53
Step:	 108 	Range:	 53
Step:	 109 	Range:	 60
Step:	 110 	Range:	 57
Step:	 111 	Range:	 58
Step:	 112 	Range:	 54
Step:	 113 	Range:	 52
Step:	 114 	Range:	 50
Step:	 115 	Range:	 52
Step:	 116 	Range:	 54
Step:	 117 	Range:	 49
Step:	 118 	Range:	 56
Step:	 119 	Range:	 58
Step:	 120 	Range:	 54
Step:	 121 	Range:	 55
Step:	 122 	Range:	 57
Step:	 123 	Range:	 54
Step:	 124 	Range:	 57
Step:	 125 	Range:	 55
Step:	 126 	Range:	 54
Step:	 127 	Range:	 51
Step:	 128 	Range:	 56
Step:	 129 	Range:	 50
Step:	 130 	Range:	 56
Step:	 131 	Range:	 55
Step:	 132 	Range:	 57
Step:	 133 	Range:	 53
Step:	 134 	Range:	 57
Step:	 135 	Range:	 58
Step:	 136 	Range:	 62
Step:	 137 	Range:	 57
Step:	 138 	Range:	 57
Step:	 139 	Range:	 60
Step:	 140 	Range:	 62
Step:	 141 	Range:	 64
Step:	 142 	Range:	 72
Step:	 143 	Range:	 74
Step:	 144 	Range:	 80
Step:	 145 	Range:	 86
Step:	 146 	Range:	 92
Step:	 147 	Range:	 96
Step:	 148 	Range:	 88
Step:	 149 	Range:	 72
Step:	 150 	Range:	 74
Step:	 151 	Range:	 112
Step:	 152 	Range:	 136
Step:	 153 	Range:	 149
Step:	 154 	Range:	 155
Step:	 155 	Range:	 159
Step:	 156 	Range:	 156
Step:	 157 	Range:	 163
Step:	 158 	Range:	 161
Step:	 159 	Range:	 160
Step:	 160 	Range:	 165
Step:	 161 	Range:	 162
Step:	 162 	Range:	 162
Step:	 163 	Range:	 159
Step:	 164 	Range:	 163
Step:	 165 	Range:	 160
Step:	 166 	Range:	 158
Step:	 167 	Range:	 153
Step:	 168 	Range:	 156
Step:	 169 	Range:	 147
Step:	 170 	Range:	 145
Step:	 171 	Range:	 139
Step:	 172 	Range:	 137
Step:	 173 	Range:	 127
Step:	 174 	Range:	 123
Step:	 175 	Range:	 117
Step:	 176 	Range:	 114
Step:	 177 	Range:	 114
Step:	 178 	Range:	 255
Step:	 179 	Range:	 255
Step:	 180 	Range:	 255
Step:	 181 	Range:	 255
Step:	 182 	Range:	 255
Step:	 183 	Range:	 255
Step:	 184 	Range:	 255
Step:	 185 	Range:	 255
Step:	 186 	Range:	 255
Step:	 187 	Range:	 255
Step:	 188 	Range:	 255
Step:	 189 	Range:	 255
Step:	 190 	Range:	 72
Step:	 191 	Range:	 72
Step:	 192 	Range:	 63
Step:	 193 	Range:	 71
Step:	 194 	Range:	 67
Step:	 195 	Range:	 69
Step:	 196 	Range:	 68
Step:	 197 	Range:	 68
Step:	 198 	Range:	 66
Step:	 199 	Range:	 63
start experiment
Step:	 0 	Range:	 60
Step:	 1 	Range:	 64
Step:	 2 	Range:	 63
Step:	 3 	Range:	 63
Step:	 4 	Range:	 62
Step:	 5 	Range:	 68
Step:	 6 	Range:	 69
Step:	 7 	Range:	 72
Step:	 8 	Range:	 69
Step:	 9 	Range:	 73
Step:	 10 	Range:	 73
Step:	 11 	Range:	 73
Step:	 12 	Range:	 74
Step:	 13 	Range:	 255
Step:	 14 	Range:	 255
Step:	 15 	Range:	 255
Step:	 16 	Range:	 255
Step:	 17 	Range:	 255
Step:	 18 	Range:	 255
Step:	 19 	Range:	 255
Step:	 20 	Range:	 255
Step:	 21 	Range:	 255
Step:	 22 	Range:	 255
Step:	 23 	Range:	 255
Step:	 24 	Range:	 106
Step:	 25 	Range:	 107
Step:	 26 	Range:	 110
Step:	 27 	Range:	 118
Step:	 28 	Range:	 125
Step:	 29 	Range:	 127
Step:	 30 	Range:	 125
Step:	 31 	Range:	 134
Step:	 32 	Range:	 143
Step:	 33 	Range:	 147
Step:	 34 	Range:	 149
Step:	 35 	Range:	 157
Step:	 36 	Range:	 150
Step:	 37 	Range:	 157
Step:	 38 	Range:	 160
Step:	 39 	Range:	 165
Step:	 40 	Range:	 161
Step:	 41 	Range:	 163
Step:	 42 	Range:	 162
Step:	 43 	Range:	 160
Step:	 44 	Range:	 162
Step:	 45 	Range:	 163
Step:	 46 	Range:	 159
Step:	 47 	Range:	 156
Step:	 48 	Range:	 157
Step:	 49 	Range:	 154
Step:	 50 	Range:	 151
Step:	 51 	Range:	 133
Step:	 52 	Range:	 94
Step:	 53 	Range:	 77
Step:	 54 	Range:	 87
Step:	 55 	Range:	 97
Step:	 56 	Range:	 102
Step:	 57 	Range:	 103
Step:	 58 	Range:	 95
Step:	 59 	Range:	 99
Step:	 60 	Range:	 90
Step:	 61 	Range:	 81
Step:	 62 	Range:	 75
Step:	 63 	Range:	 71
Step:	 64 	Range:	 71
Step:	 65 	Range:	 70
Step:	 66 	Range:	 65
Step:	 67 	Range:	 66
Step:	 68 	Range:	 63
Step:	 69 	Range:	 58
Step:	 70 	Range:	 59
Step:	 71 	Range:	 58
Step:	 72 	Range:	 54
Step:	 73 	Range:	 59
Step:	 74 	Range:	 56
Step:	 75 	Range:	 55
Step:	 76 	Range:	 58
Step:	 77 	Range:	 61
Step:	 78 	Range:	 57
Step:	 79 	Range:	 54
Step:	 80 	Range:	 55
Step:	 81 	Range:	 53
Step:	 82 	Range:	 52
Step:	 83 	Range:	 55
Step:	 84 	Range:	 52
Step:	 85 	Range:	 56
Step:	 86 	Range:	 54
Step:	 87 	Range:	 54
Step:	 88 	Range:	 53
Step:	 89 	Range:	 52
Step:	 90 	Range:	 48
Step:	 91 	Range:	 53
Step:	 92 	Range:	 49
Step:	 93 	Range:	 53
Step:	 94 	Range:	 52
Step:	 95 	Range:	 54
Step:	 96 	Range:	 52
Step:	 97 	Range:	 53
Step:	 98 	Range:	 44
Step:	 99 	Range:	 38
Step:	 100 	Range:	 38
Step:	 101 	Range:	 38
Step:	 102 	Range:	 38
Step:	 103 	Range:	 39
Step:	 104 	Range:	 41
Step:	 105 	Range:	 42
Step:	 106 	Range:	 53
Step:	 107 	Range:	 57
Step:	 108 	Range:	 53
Step:	 109 	Range:	 51
Step:	 110 	Range:	 52
Step:	 111 	Range:	 52
Step:	 112 	Range:	 50
Step:	 113 	Range:	 52
Step:	 114 	Range:	 53
Step:	 115 	Range:	 57
Step:	 116 	Range:	 49
Step:	 117 	Range:	 54
Step:	 118 	Range:	 53
Step:	 119 	Range:	 57
Step:	 120 	Range:	 50
Step:	 121 	Range:	 55
Step:	 122 	Range:	 51
Step:	 123 	Range:	 52
Step:	 124 	Range:	 53
Step:	 125 	Range:	 52
Step:	 126 	Range:	 52
Step:	 127 	Range:	 50
Step:	 128 	Range:	 52
Step:	 129 	Range:	 54
Step:	 130 	Range:	 53
Step:	 131 	Range:	 53
Step:	 132 	Range:	 49
Step:	 133 	Range:	 48
Step:	 134 	Range:	 52
Step:	 135 	Range:	 52
Step:	 136 	Range:	 54
Step:	 137 	Range:	 56
Step:	 138 	Range:	 59
Step:	 139 	Range:	 59
Step:	 140 	Range:	 66
Step:	 141 	Range:	 63
Step:	 142 	Range:	 66
Step:	 143 	Range:	 72
Step:	 144 	Range:	 79
Step:	 145 	Range:	 88
Step:	 146 	Range:	 90
Step:	 147 	Range:	 88
Step:	 148 	Range:	 85
Step:	 149 	Range:	 65
Step:	 150 	Range:	 75
Step:	 151 	Range:	 112
Step:	 152 	Range:	 131
Step:	 153 	Range:	 147
Step:	 154 	Range:	 151
Step:	 155 	Range:	 156
Step:	 156 	Range:	 162
Step:	 157 	Range:	 158
Step:	 158 	Range:	 158
Step:	 159 	Range:	 162
Step:	 160 	Range:	 162
Step:	 161 	Range:	 160
Step:	 162 	Range:	 160
Step:	 163 	Range:	 160
Step:	 164 	Range:	 162
Step:	 165 	Range:	 160
Step:	 166 	Range:	 158
Step:	 167 	Range:	 157
Step:	 168 	Range:	 153
Step:	 169 	Range:	 151
Step:	 170 	Range:	 142
Step:	 171 	Range:	 139
Step:	 172 	Range:	 132
Step:	 173 	Range:	 130
Step:	 174 	Range:	 120
Step:	 175 	Range:	 122
Step:	 176 	Range:	 114
Step:	 177 	Range:	 108
Step:	 178 	Range:	 103
Step:	 179 	Range:	 255
Step:	 180 	Range:	 255
Step:	 181 	Range:	 255
Step:	 182 	Range:	 255
Step:	 183 	Range:	 255
Step:	 184 	Range:	 255
Step:	 185 	Range:	 255
Step:	 186 	Range:	 255
Step:	 187 	Range:	 255
Step:	 188 	Range:	 255
Step:	 189 	Range:	 255
Step:	 190 	Range:	 68
Step:	 191 	Range:	 63
Step:	 192 	Range:	 68
Step:	 193 	Range:	 68
Step:	 194 	Range:	 67
Step:	 195 	Range:	 69
Step:	 196 	Range:	 69
Step:	 197 	Range:	 66
Step:	 198 	Range:	 65
Step:	 199 	Range:	 63
start experiment
Step:	 0 	Range:	 61
Step:	 1 	Range:	 62
Step:	 2 	Range:	 62
Step:	 3 	Range:	 62
Step:	 4 	Range:	 65
Step:	 5 	Range:	 65
Step:	 6 	Range:	 72
Step:	 7 	Range:	 71
Step:	 8 	Range:	 71
Step:	 9 	Range:	 73
Step:	 10 	Range:	 71
Step:	 11 	Range:	 75
Step:	 12 	Range:	 73
Step:	 13 	Range:	 76
Step:	 14 	Range:	 255
Step:	 15 	Range:	 255
Step:	 16 	Range:	 255
Step:	 17 	Range:	 255
Step:	 18 	Range:	 255
Step:	 19 	Range:	 255
Step:	 20 	Range:	 255
Step:	 21 	Range:	 255
Step:	 22 	Range:	 255
Step:	 23 	Range:	 91
Step:	 24 	Range:	 102
Step:	 25 	Range:	 104
Step:	 26 	Range:	 110
Step:	 27 	Range:	 114
Step:	 28 	Range:	 116
Step:	 29 	Range:	 127
Step:	 30 	Range:	 128
Step:	 31 	Range:	 134
Step:	 32 	Range:	 141
Step:	 33 	Range:	 146
Step:	 34 	Range:	 147
Step:	 35 	Range:	 150
Step:	 36 	Range:	 156
Step:	 37 	Range:	 159
Step:	 38 	Range:	 159
Step:	 39 	Range:	 159
Step:	 40 	Range:	 160
Step:	 41 	Range:	 163
Step:	 42 	Range:	 158
Step:	 43 	Range:	 156
Step:	 44 	Range:	 164
Step:	 45 	Range:	 161
Step:	 46 	Range:	 159
Step:	 47 	Range:	 158
Step:	 48 	Range:	 154
Step:	 49 	Range:	 149
Step:	 50 	Range:	 150
Step:	 51 	Range:	 134
Step:	 52 	Range:	 97
Step:	 53 	Range:	 77
Step:	 54 	Range:	 90
Step:	 55 	Range:	 97
Step:	 56 	Range:	 99
Step:	 57 	Range:	 98
Step:	 58 	Range:	 98
Step:	 59 	Range:	 93
Step:	 60 	Range:	 91
Step:	 61 	Range:	 81
Step:	 62 	Range:	 79
Step:	 63 	Range:	 76
Step:	 64 	Range:	 67
Step:	 65 	Range:	 67
Step:	 66 	Range:	 63
Step:	 67 	Range:	 64
Step:	 68 	Range:	 62
Step:	 69 	Range:	 65
Step:	 70 	Range:	 60
Step:	 71 	Range:	 62
Step:	 72 	Range:	 61
Step:	 73 	Range:	 56
Step:	 74 	Range:	 56
Step:	 75 	Range:	 58
Step:	 76 	Range:	 55
Step:	 77 	Range:	 56
Step:	 78 	Range:	 55
Step:	 79 	Range:	 55
Step:	 80 	Range:	 56
Step:	 81 	Range:	 54
Step:	 82 	Range:	 55
Step:	 83 	Range:	 53
Step:	 84 	Range:	 55
Step:	 85 	Range:	 50
Step:	 86 	Range:	 54
Step:	 87 	Range:	 56
Step:	 88 	Range:	 54
Step:	 89 	Range:	 54
Step:	 90 	Range:	 53
Step:	 91 	Range:	 58
Step:	 92 	Range:	 54
Step:	 93 	Range:	 55
Step:	 94 	Range:	 57
Step:	 95 	Range:	 52
Step:	 96 	Range:	 55
Step:	 97 	Range:	 52
Step:	 98 	Range:	 45
Step:	 99 	Range:	 38
Step:	 100 	Range:	 37
Step:	 101 	Range:	 38
Step:	 102 	Range:	 35
Step:	 103 	Range:	 36
Step:	 104 	Range:	 39
Step:	 105 	Range:	 47
Step:	 106 	Range:	 47
Step:	 107 	Range:	 52
Step:	 108 	Range:	 50
Step:	 109 	Range:	 51
Step:	 110 	Range:	 56
Step:	 111 	Range:	 54
Step:	 112 	Range:	 51
Step:	 113 	Range:	 53
Step:	 114 	Range:	 48
Step:	 115 	Range:	 49
Step:	 116 	Range:	 51
Step:	 117 	Range:	 53
Step:	 118 	Range:	 55
Step:	 119 	Range:	 53
Step:	 120 	Range:	 50
Step:	 121 	Range:	 53
Step:	 122 	Range:	 48
Step:	 123 	Range:	 58
Step:	 124 	Range:	 49
Step:	 125 	Range:	 57
Step:	 126 	Range:	 53
Step:	 127 	Range:	 51
Step:	 128 	Range:	 57
Step:	 129 	Range:	 49
Step:	 130 	Range:	 52
Step:	 131 	Range:	 53
Step:	 132 	Range:	 56
Step:	 133 	Range:	 50
Step:	 134 	Range:	 53
Step:	 135 	Range:	 57
Step:	 136 	Range:	 59
Step:	 137 	Range:	 57
Step:	 138 	Range:	 54
Step:	 139 	Range:	 55
Step:	 140 	Range:	 61
Step:	 141 	Range:	 66
Step:	 142 	Range:	 70
Step:	 143 	Range:	 75
Step:	 144 	Range:	 81
Step:	 145 	Range:	 85
Step:	 146 	Range:	 91
Step:	 147 	Range:	 91
Step:	 148 	Range:	 84
Step:	 149 	Range:	 69
Step:	 150 	Range:	 77
Step:	 151 	Range:	 112
Step:	 152 	Range:	 136
Step:	 153 	Range:	 148
Step:	 154 	Range:	 151
Step:	 155 	Range:	 156
Step:	 156 	Range:	 159
Step:	 157 	Range:	 159
Step:	 158 	Range:	 164
Step:	 159 	Range:	 162
Step:	 160 	Range:	 160
Step:	 161 	Range:	 160
Step:	 162 	Range:	 165
Step:	 163 	Range:	 161
Step:	 164 	Range:	 161
Step:	 165 	Range:	 156
Step:	 166 	Range:	 155
Step:	 167 	Range:	 153
Step:	 168 	Range:	 157
Step:	 169 	Range:	 152
Step:	 170 	Range:	 137
Step:	 171 	Range:	 139
Step:	 172 	Range:	 136
Step:	 173 	Range:	 129
Step:	 174 	Range:	 122
Step:	 175 	Range:	 118
Step:	 176 	Range:	 116
Step:	 177 	Range:	 108
Step:	 178 	Range:	 255
Step:	 179 	Range:	 255
Step:	 180 	Range:	 255
Step:	 181 	Range:	 255
Step:	 182 	Range:	 255
Step:	 183 	Range:	 255
Step:	 184 	Range:	 255
Step:	 185 	Range:	 255
Step:	 186 	Range:	 255
Step:	 187 	Range:	 255
Step:	 188 	Range:	 255
Step:	 189 	Range:	 255
Step:	 190 	Range:	 69
Step:	 191 	Range:	 72
Step:	 192 	Range:	 66
Step:	 193 	Range:	 72
Step:	 194 	Range:	 73
Step:	 195 	Range:	 68
Step:	 196 	Range:	 63
Step:	 197 	Range:	 68
Step:	 198 	Range:	 61
Step:	 199 	Range:	 62
start experiment
Step:	 0 	Range:	 62
Step:	 1 	Range:	 61
Step:	 2 	Range:	 63
Step:	 3 	Range:	 64
Step:	 4 	Range:	 65
Step:	 5 	Range:	 65
Step:	 6 	Range:	 67
Step:	 7 	Range:	 68
Step:	 8 	Range:	 70
Step:	 9 	Range:	 73
Step:	 10 	Range:	 73
Step:	 11 	Range:	 74
Step:	 12 	Range:	 76
Step:	 13 	Range:	 74
Step:	 14 	Range:	 255
Step:	 15 	Range:	 255
Step:	 16 	Range:	 255
Step:	 17 	Range:	 255
Step:	 18 	Range:	 255
Step:	 19 	Range:	 255
Step:	 20 	Range:	 255
Step:	 21 	Range:	 255
Step:	 22 	Range:	 255
Step:	 23 	Range:	 97
Step:	 24 	Range:	 107
Step:	 25 	Range:	 111
Step:	 26 	Range:	 113
Step:	 27 	Range:	 115
Step:	 28 	Range:	 119
Step:	 29 	Range:	 125
Step:	 30 	Range:	 129
Step:	 31 	Range:	 137
Step:	 32 	Range:	 141
Step:	 33 	Range:	 144
Step:	 34 	Range:	 146
Step:	 35 	Range:	 151
Step:	 36 	Range:	 154
Step:	 37 	Range:	 153
Step:	 38 	Range:	 157
Step:	 39 	Range:	 157
Step:	 40 	Range:	 163
Step:	 41 	Range:	 156
Step:	 42 	Range:	 159
Step:	 43 	Range:	 157
Step:	 44 	Range:	 158
Step:	 45 	Range:	 156
Step:	 46 	Range:	 158
Step:	 47 	Range:	 157
Step:	 48 	Range:	 156
Step:	 49 	Range:	 151
Step:	 50 	Range:	 147
Step:	 51 	Range:	 133
Step:	 52 	Range:	 92
Step:	 53 	Range:	 77
Step:	 54 	Range:	 91
Step:	 55 	Range:	 105
Step:	 56 	Range:	 103
Step:	 57 	Range:	 102
Step:	 58 	Range:	 96
Step:	 59 	Range:	 97
Step:	 60 	Range:	 88
Step:	 61 	Range:	 83
Step:	 62 	Range:	 80
Step:	 63 	Range:	 72
Step:	 64 	Range:	 69
Step:	 65 	Range:	 64
Step:	 66 	Range:	 67
Step:	 67 	Range:	 63
Step:	 68 	Range:	 59
Step:	 69 	Range:	 62
Step:	 70 	Range:	 65
Step:	 71 	Range:	 60
Step:	 72 	Range:	 61
Step:	 73 	Range:	 61
Step:	 74 	Range:	 56
Step:	 75 	Range:	 56
Step:	 76 	Range:	 61
Step:	 77 	Range:	 61
Step:	 78 	Range:	 57
Step:	 79 	Range:	 50
Step:	 80 	Range:	 59
Step:	 81 	Range:	 57
Step:	 82 	Range:	 52
Step:	 83 	Range:	 53
Step:	 84 	Range:	 57
Step:	 85 	Range:	 57
Step:	 86 	Range:	 58
Step:	 87 	Range:	 54
Step:	 88 	Range:	 54
Step:	 89 	Range:	 56
Step:	 90 	Range:	 53
Step:	 91 	Range:	 56
Step:	 92 	Range:	 51
Step:	 93 	Range:	 53
Step:	 94 	Range:	 53
Step:	 95 	Range:	 52
Step:	 96 	Range:	 53
Step:	 97 	Range:	 54
Step:	 98 	Range:	 42
Step:	 99 	Range:	 40
Step:	 100 	Range:	 40
Step:	 101 	Range:	 35
Step:	 102 	Range:	 36
Step:	 103 	Range:	 38
Step:	 104 	Range:	 39
Step:	 105 	Range:	 41
Step:	 106 	Range:	 54
Step:	 107 	Range:	 53
Step:	 108 	Range:	 53
Step:	 109 	Range:	 50
Step:	 110 	Range:	 54
Step:	 111 	Range:	 49
Step:	 112 	Range:	 51
Step:	 113 	Range:	 54
Step:	 114 	Range:	 52
Step:	 115 	Range:	 52
Step:	 116 	Range:	 55
Step:	 117 	Range:	 50
Step:	 118 	Range:	 54
Step:	 119 	Range:	 51
Step:	 120 	Range:	 51
Step:	 121 	Range:	 52
Step:	 122 	Range:	 56
Step:	 123 	Range:	 51
Step:	 124 	Range:	 54
Step:	 125 	Range:	 52
Step:	 126 	Range:	 51
Step:	 127 	Range:	 52
Step:	 128 	Range:	 52
Step:	 129 	Range:	 52
Step:	 130 	Range:	 48
Step:	 131 	Range:	 45
Step:	 132 	Range:	 52
Step:	 133 	Range:	 53
Step:	 134 	Range:	 52
Step:	 135 	Range:	 55
Step:	 136 	Range:	 49
Step:	 137 	Range:	 50
Step:	 138 	Range:	 55
Step:	 139 	Range:	 57
Step:	 140 	Range:	 61
Step:	 141 	Range:	 65
Step:	 142 	Range:	 70
Step:	 143 	Range:	 72
Step:	 144 	Range:	 78
Step:	 145 	Range:	 84
Step:	 146 	Range:	 88
Step:	 147 	Range:	 94
Step:	 148 	Range:	 85
Step:	 149 	Range:	 67
Step:	 150 	Range:	 80
Step:	 151 	Range:	 116
Step:	 152 	Range:	 140
Step:	 153 	Range:	 148
Step:	 154 	Range:	 156
Step:	 155 	Range:	 159
Step:	 156 	Range:	 160
Step:	 157 	Range:	 163
Step:	 158 	Range:	 163
Step:	 159 	Range:	 162
Step:	 160 	Range:	 164
Step:	 161 	Range:	 166
Step:	 162 	Range:	 161
Step:	 163 	Range:	 167
Step:	 164 	Range:	 157
Step:	 165 	Range:	 162
Step:	 166 	Range:	 160
Step:	 167 	Range:	 154
Step:	 168 	Range:	 148
Step:	 169 	Range:	 148
Step:	 170 	Range:	 144
Step:	 171 	Range:	 138
Step:	 172 	Range:	 136
Step:	 173 	Range:	 135
Step:	 174 	Range:	 121
Step:	 175 	Range:	 118
Step:	 176 	Range:	 114
Step:	 177 	Range:	 114
Step:	 178 	Range:	 255
Step:	 179 	Range:	 255
Step:	 180 	Range:	 255
Step:	 181 	Range:	 255
Step:	 182 	Range:	 255
Step:	 183 	Range:	 255
Step:	 184 	Range:	 255
Step:	 185 	Range:	 255
Step:	 186 	Range:	 255
Step:	 187 	Range:	 255
Step:	 188 	Range:	 255
Step:	 189 	Range:	 71
Step:	 190 	Range:	 71
Step:	 191 	Range:	 69
Step:	 192 	Range:	 70
Step:	 193 	Range:	 69
Step:	 194 	Range:	 71
Step:	 195 	Range:	 65
Step:	 196 	Range:	 62
Step:	 197 	Range:	 65
Step:	 198 	Range:	 63
Step:	 199 	Range:	 63

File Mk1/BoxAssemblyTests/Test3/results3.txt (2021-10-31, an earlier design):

Table Homing
Moving table to upper limit
Moving table to upper limit - done
Table retract from upper limit
Table retract from upper limit - done
Table seek upper limit
Table seek upper limit - done
Table Homed
Poker Homing
Fully retract and confirm sensor reset - done
Stage Poker and confirm sensor available - done
Fully retract poker ready for table movement - done
Poker Homed
ConfirmFirstMeasureToSideOfTable()
Table measured at :134
ConfirmFirstMeasureToSideOfTable() - done
MoveTableToScanStartPosition()
MoveTableToScanStartPosition() - done
Press confirm to begin scan?
PerformScan
Revolution 0
0:0 touched True angle 106
0:1 touched True angle 106
0:2 touched True angle 106
0:3 touched True angle 105
0:4 touched True angle 101
0:5 touched False angle 70
0:6 touched False angle 70
0:7 touched False angle 70
0:8 touched False angle 70
0:9 touched False angle 70
0:10 touched False angle 70
0:11 touched False angle 70
0:12 touched False angle 70
0:13 touched False angle 70
0:14 touched True angle 70
0:15 touched True angle 70
0:16 touched True angle 73
0:17 touched True angle 72
0:18 touched True angle 75
0:19 touched True angle 74
0:20 touched True angle 77
0:21 touched True angle 78
0:22 touched True angle 78
0:23 touched True angle 78
0:24 touched True angle 78
0:25 touched False angle 70
0:26 touched False angle 70
0:27 touched False angle 70
0:28 touched False angle 70
0:29 touched True angle 114
0:30 touched True angle 114
0:31 touched True angle 113
0:32 touched True angle 114
0:33 touched True angle 113
0:34 touched True angle 113
0:35 touched True angle 112
0:36 touched True angle 112
0:37 touched True angle 111
0:38 touched True angle 111
0:39 touched True angle 111
0:40 touched True angle 111
0:41 touched True angle 110
0:42 touched True angle 110
0:43 touched True angle 110
0:44 touched True angle 110
0:45 touched True angle 109
0:46 touched True angle 109
0:47 touched True angle 108
0:48 touched True angle 108
0:49 touched True angle 108
0:50 touched True angle 107
Revolution 1
1:0 touched True angle 107
1:1 touched True angle 106
1:2 touched True angle 106
1:3 touched True angle 105
1:4 touched False angle 70
1:5 touched False angle 70
1:6 touched False angle 70
1:7 touched False angle 70
1:8 touched False angle 70
1:9 touched False angle 70
1:10 touched False angle 70
1:11 touched False angle 70
1:12 touched False angle 70
1:13 touched False angle 70
1:14 touched True angle 70
1:15 touched True angle 70
1:16 touched True angle 73
1:17 touched True angle 74
1:18 touched True angle 75
1:19 touched True angle 77
1:20 touched True angle 77
1:21 touched True angle 78
1:22 touched True angle 79
1:23 touched True angle 79
1:24 touched False angle 70
1:25 touched False angle 70
1:26 touched False angle 70
1:27 touched False angle 70
1:28 touched False angle 70
1:29 touched True angle 114
1:30 touched True angle 114
1:31 touched True angle 114
1:32 touched True angle 114
1:33 touched True angle 113
1:34 touched True angle 113
1:35 touched True angle 112
1:36 touched True angle 112
1:37 touched True angle 112
1:38 touched True angle 112
1:39 touched True angle 111
1:40 touched True angle 111
1:41 touched True angle 111
1:42 touched True angle 110
1:43 touched True angle 110
1:44 touched True angle 110
1:45 touched True angle 110
1:46 touched True angle 109
1:47 touched True angle 108
1:48 touched True angle 108
1:49 touched True angle 108
1:50 touched True angle 108
Revolution 2
2:0 touched True angle 107
2:1 touched True angle 107
2:2 touched True angle 106
2:3 touched True angle 106
2:4 touched False angle 70
2:5 touched False angle 70
2:6 touched False angle 70
2:7 touched False angle 70
2:8 touched False angle 70
2:9 touched False angle 70
2:10 touched False angle 70
2:11 touched False angle 70
2:12 touched False angle 70
2:13 touched False angle 70
2:14 touched True angle 71
2:15 touched True angle 70
2:16 touched True angle 73
2:17 touched True angle 74
2:18 touched True angle 75
2:19 touched True angle 77
2:20 touched True angle 77
2:21 touched True angle 79
2:22 touched True angle 79
2:23 touched True angle 79
2:24 touched False angle 70
2:25 touched False angle 70
2:26 touched False angle 70
2:27 touched False angle 70
2:28 touched False angle 70
2:29 touched True angle 114
2:30 touched True angle 115
2:31 touched True angle 114
2:32 touched True angle 114
2:33 touched True angle 113
2:34 touched True angle 113
2:35 touched True angle 112
2:36 touched True angle 112
2:37 touched True angle 112
2:38 touched True angle 112
2:39 touched True angle 111
2:40 touched True angle 111
2:41 touched True angle 111
2:42 touched True angle 111
2:43 touched True angle 110
2:44 touched True angle 110
2:45 touched True angle 110
2:46 touched True angle 109
2:47 touched True angle 109
2:48 touched True angle 108
2:49 touched True angle 108
2:50 touched True angle 108
Revolution 3
3:0 touched True angle 107
3:1 touched True angle 107
3:2 touched True angle 106
3:3 touched True angle 106
3:4 touched False angle 70
3:5 touched False angle 70
3:6 touched False angle 70
3:7 touched False angle 70
3:8 touched False angle 70
3:9 touched False angle 70
3:10 touched False angle 70
3:11 touched False angle 70
3:12 touched False angle 70
3:13 touched False angle 70
3:14 touched True angle 71
3:15 touched True angle 71
3:16 touched True angle 74
3:17 touched True angle 75
3:18 touched True angle 75
3:19 touched True angle 77
3:20 touched True angle 77
3:21 touched True angle 79
3:22 touched True angle 79
3:23 touched True angle 79
3:24 touched False angle 70
3:25 touched False angle 70
3:26 touched False angle 70
3:27 touched False angle 70
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

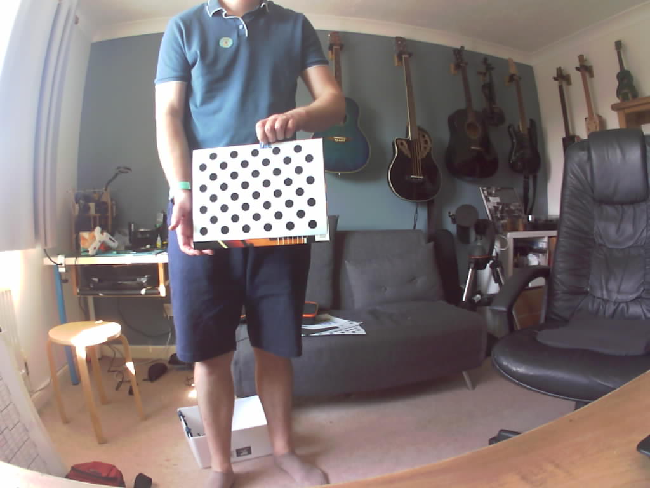
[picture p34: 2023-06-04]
Mk5/Code/07_Calibration_00/run_010/capture_001.jpg

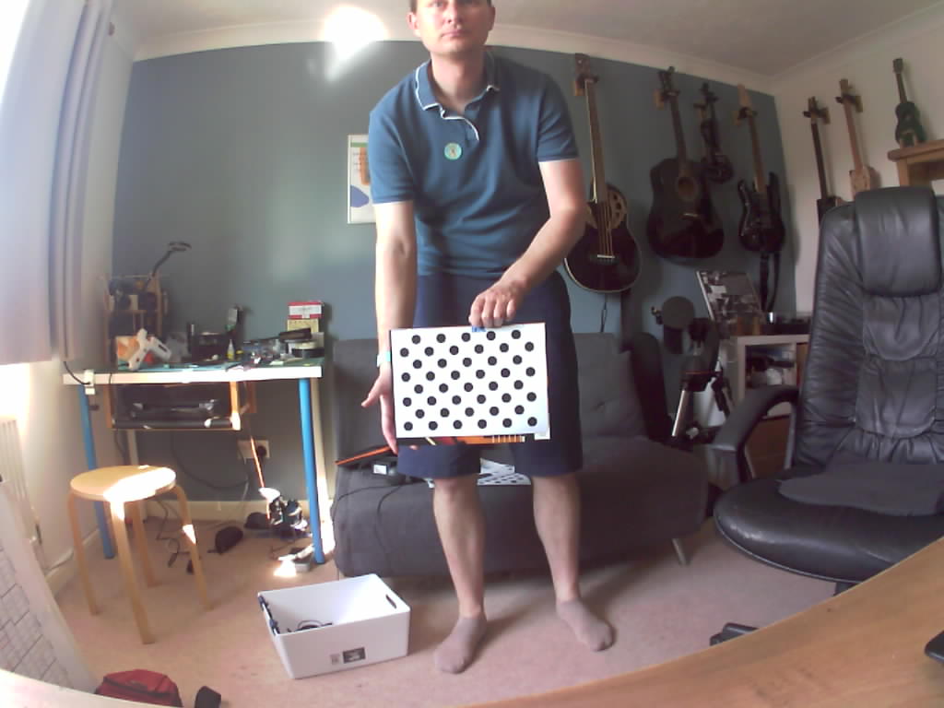
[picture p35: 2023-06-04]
Mk5/Code/07_Calibration_00/run_010/capture_004.jpg

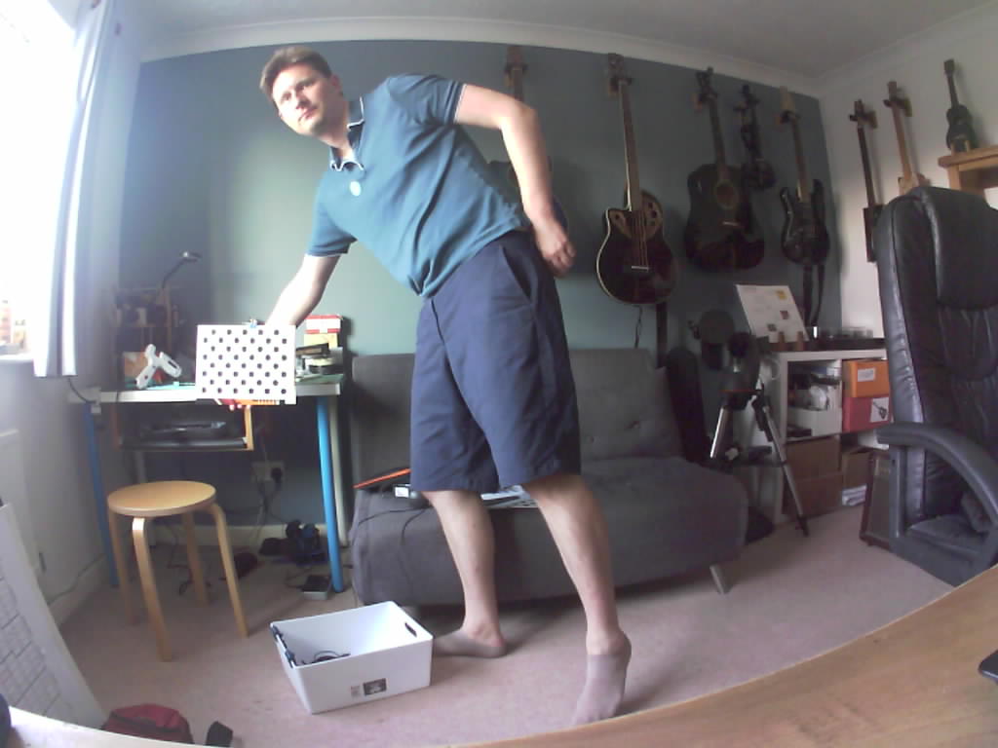
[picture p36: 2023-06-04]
Mk5/Code/07_Calibration_00/run_011/capture_002.jpg

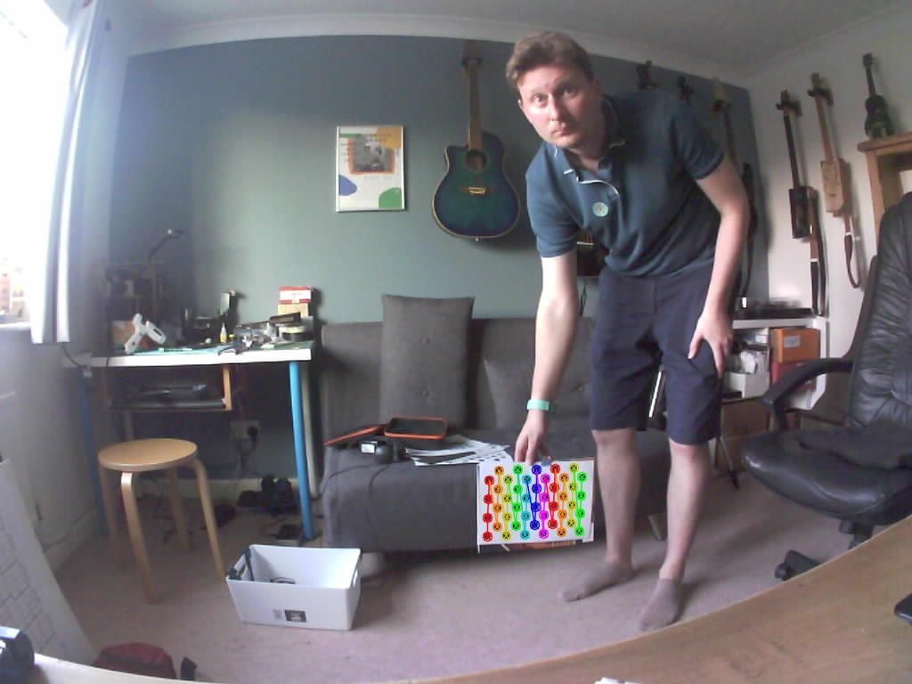
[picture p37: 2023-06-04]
Mk5/Code/07_Calibration_00/good_with_markup/capture_022_markup.jpg

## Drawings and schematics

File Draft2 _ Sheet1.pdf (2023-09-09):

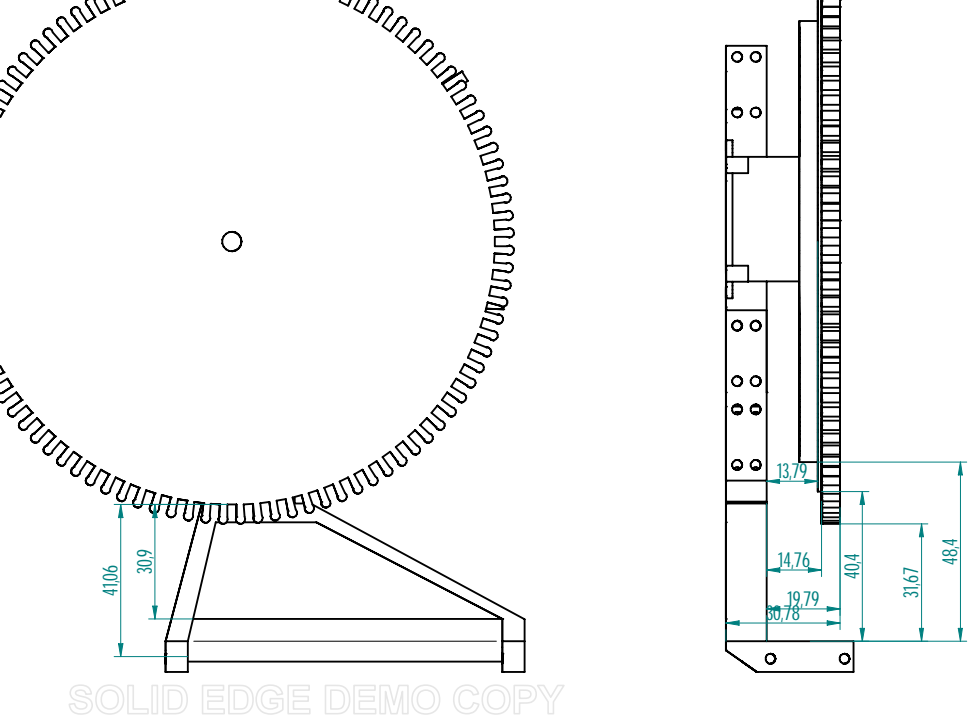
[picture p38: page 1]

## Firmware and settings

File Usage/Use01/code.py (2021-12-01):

# First usage to measure a real shape
# Prototype finish when no measurements for a whole revolution
# includes quick advance

import time
import board
import digitalio
import pwmio
from digitalio import DigitalInOut, Direction, Pull
from adafruit_motor import stepper, servo


# Servo control
servoPositionA = 145 # All the way back from the table
servoPositionB = 139 # Near edge of table
servoPositionC = 135 # Touching edge of table
servoPositionD = 70 # At full reach across the table
servoPositionE = 115 # skip measurements before this (nothing outside this)

servoCurrentTarget = servoPositionB

maxTableRevolutions = 75

# create a PWMOut object on Pin A2.# Using small spiral to calibrate servo
# includes quick advance

import time
import board
import digitalio
import pwmio
from digitalio import DigitalInOut, Direction, Pull
from adafruit_motor import stepper, servo


# Servo control
servoPositionA = 145 # All the way back from the table
servoPositionB = 139 # Near edge of table
servoPositionC = 135 # Touching edge of table
servoPositionD = 70 # At full reach across the table
servoPositionE = 120 # skip measurements before this (nothing outside this)

servoCurrentTarget = servoPositionB

# create a PWMOut object on Pin A2.
pwm = pwmio.PWMOut(board.GP2, duty_cycle=2 ** 15, frequency=50)
my_servo = servo.Servo(pwm)

# Stepper motor setup
DELAY = 0.1  # fastest is ~ 0.004, 0.01 is still very smooth, gets steppy after that
STEPS = 200  # this is a full 360º
coils = (
    DigitalInOut(board.GP21),  # A1
    DigitalInOut(board.GP20),  # A2
    DigitalInOut(board.GP19),  # B1
    DigitalInOut(board.GP18),  # B2
)
for coil in coils:
    coil.direction = Direction.OUTPUT

stepper_motor = stepper.StepperMotor(
    coils[0], coils[1], coils[2], coils[3], microsteps=None
)

stepperAdvanceFromHome = 40 * 100


button12 = digitalio.DigitalInOut(board.GP12)
button12.switch_to_input(pull=digitalio.Pull.UP)
button13 = digitalio.DigitalInOut(board.GP13)
button13.switch_to_input(pull=digitalio.Pull.UP)

# Go / OK / start button
button14 = digitalio.DigitalInOut(board.GP14)
button14.switch_to_input(pull=digitalio.Pull.UP)

# Electronic break button - press if the robotics are out of range / control
button15 = digitalio.DigitalInOut(board.GP15)
button15.switch_to_input(pull=digitalio.Pull.UP)

photoSensorPin2 = digitalio.DigitalInOut(board.GP3)
photoSensorPin2.switch_to_input(pull=digitalio.Pull.UP)

led = DigitalInOut(board.LED)
led.direction = Direction.OUTPUT
led.value = True

def blink(times):
    for _ in range(times):
        led.value = False
        time.sleep(0.1)
        led.value = True
        time.sleep(0.1)

def Panic():
    # Park Servo
    print("PANIC")
    stepper_motor.release()
    # Don't use MoveServo as that calls CheckEBreak
    my_servo.angle = servoPositionB
    while True:
        if button14.value == False:
            print("OK button releases panic")
            break
        time.sleep(0.1)

def CheckEBreak():
    # Button 15 is the EBreak - if this is pressed then:
    # Send Servo at safe value
    # Wait for OK
    if button15.value == False:
        Panic()

def CheckServoPositionIsInRangeAndPanic(newTargetAngle):
    # This assert cannot be the result of mistiming and should not be re-tried
    if newTargetAngle > servoPositionA:
        print("** ERROR ** ServoPosition %s is beyond full retract of arm",str(newTargetAngle))    
        Panic()
    # This assert cannot be the result of mistiming and should not be re-tried
    if newTargetAngle < servoPositionD:
        print("** ERROR ** ServoPosition %s is beyond full extent of arm",str(newTargetAngle))
        Panic()        

def MoveServo(newTargetAngle):
    global servoCurrentTarget
    CheckEBreak()
    CheckServoPositionIsInRangeAndPanic(newTargetAngle)

    servoCurrentTarget = newTargetAngle
    my_servo.angle = servoCurrentTarget
    for _ in range(10):
        CheckEBreak()
        time.sleep(0.025)

    

def StepTableUpOneStepWithDelay():
    stepper_motor.onestep(direction=stepper.BACKWARD,style=stepper.DOUBLE) # BACKWARDs is table up
    time.sleep(0.002)

def StepTableDownOneStepWithDelay():
    stepper_motor.onestep(direction=stepper.FORWARD,style=stepper.DOUBLE) # FORWARDs is table down
    time.sleep(0.002)

def TableIsAtUpperStop():
    return button13.value == False

def TableIsAtLowerStop():
    return button12.value == False


def TableHomeCycle():
    print("Table Homing")

    # Move table up until upper limit reached
    print("Moving table to upper limit")
    while not TableIsAtUpperStop():
        CheckEBreak()
        #Move stepper clockwise (up) fast
        StepTableUpOneStepWithDelay()
    print("Moving table to upper limit - done")

    print("Table retract from upper limit")
    # Move slowly down until upper limit switch releases
    while TableIsAtUpperStop():
        CheckEBreak()
        #Move stepper anticlockwise (down) slow
        StepTableDownOneStepWithDelay()
        #time.sleep(0.004) # extra delay to slow speed
    print("Table retract from upper limit - done")

    print("Table seek upper limit")
    # Move slowly up until upper limit switch presses
    while not TableIsAtUpperStop():
        CheckEBreak()
        #Move stepper clockwise (up) slow
        StepTableUpOneStepWithDelay()
        #time.sleep(0.004) # extra delay to slow speed
    print("Table seek upper limit - done")

    print("Table Homed")
    # disable coils
    stepper_motor.release()

    return True

def MoveTableToScanStartPosition():
    print("MoveTableToScanStartPosition()")
    CheckEBreak()

    # This assert cannot be the result of mistiming and should not be re-tried
    # This can be wrong if the table has been nudged away from the switch
    if not TableIsAtUpperStop():
        print("Table not at upper stop?")
        return False
    
    for _ in range(stepperAdvanceFromHome):
        StepTableDownOneStepWithDelay()
        CheckEBreak()
        # This assert cannot be the result of mistiming and should not be re-tried
        if TableIsAtLowerStop():
            print("Table hit lower stop!?")
            Panic()
            return False

    # disable coils
    stepper_motor.release()
    print("MoveTableToScanStartPosition() - done")
    return True

def MovePokerToNearTableEdge():
    # Move poker to be near the edge of the table, but not touching
    #print("MovePokerToNearTableEdge")
    MoveServo(servoPositionB)

def MovePokerToAdvancePositionOverTable():
    # Move poker to beyond the table edge, but before any expected reading
    MoveServo(servoPositionE)
    time.sleep(0.5)

def FullyRetractPokerAndCheckSensor():
    CheckEBreak()
    #print("FullyRetractPoker")
    # Change servo to value X
    pokerCanTellUsWhenWeAreFullyRetracted = PokerHasTouched()

    MoveServo(servoPositionA)
    
    if pokerCanTellUsWhenWeAreFullyRetracted:
        retryCount = 0
        while not PokerIsReset() and retryCount < 5:
            MoveServo(servoPositionA)
            retryCount = retryCount + 1
                
        if not PokerIsReset():
            print("** Error waiting for Poker to fully retract from PokerHasTouched position ")
            Panic()
    else:
        # Wait half a second for servo to more
        time.sleep(0.50)
        if not PokerIsReset():
            print("Poker did not reset within 0.5 - second chance...")
            MoveServo(servoPositionB)
            MoveServo(servoPositionA)
            time.sleep(0.50)

    return PokerIsReset()

def PokerHasNotTouched():
    # Sensor open means not touched
    return photoSensorPin2.value == False # False is open

def PokerHasTouched():
    # Sensor closed means not touched
    return photoSensorPin2.value == True # True is closed

def PokerIsReset():
    return PokerHasNotTouched()



def TakeMeasurement(allowFastforward = True):
    global servoCurrentTarget

    #print("Measuring")

    ok = FullyRetractPokerAndCheckSensor()
    if not ok : 
        print("FullyRetractPokerAndCheckSensor at start of TakeMeasurement() failed - second chance...")
        ok = FullyRetractPokerAndCheckSensor()
        if not ok : 
            print("** ERROR ** TakeMeasurement() FullyRetractPoker() did not succeed in expected time")
            return False, False, 0

    # Move closer to save time
    # Nothing should register before servoPositionE
    if (allowFastforward):
        MovePokerToAdvancePositionOverTable()

    if PokerHasTouched():
        print("** Warning** When staging poker, touch sensor was triggered - attempting another reset...")
        ok = FullyRetractPokerAndCheckSensor()
        if not ok or PokerHasTouched():
            print("** ERROR ** TakeMeasurement() When staging poker, touch sensor was triggered - recovery failed")
            return False, False, 0

    # ignore limit for now
    # print("Measuring - starting")
    measureAngle = servoCurrentTarget
    hasTouched = False

    while not hasTouched:
        measureAngle = measureAngle - 1
        MoveServo(measureAngle)
        hasTouched = PokerHasTouched()
        if measureAngle == servoPositionD:
            break

    #print("Measuring - done")

    ok = FullyRetractPokerAndCheckSensor()
    if not ok : 
        print("** ERROR ** TakeMeasurement() FullyRetractPoker() did not succeed after measurement on first attempt - 2nd chance")    
        ok = FullyRetractPokerAndCheckSensor()
        if not ok : 
            print("** ERROR ** TakeMeasurement() FullyRetractPoker() did not succeed")    
            return False, False, 0

    return ok, hasTouched, measureAngle


def ConfirmFirstMeasureToSideOfTable():
    print("ConfirmFirstMeasureToSideOfTable()")
    allowFastFwd = False # table will be in the way, so cannot sneak in to reduced radius of measurement
    ok, hasTouched, measureAngle = TakeMeasurement(allowFastFwd)

    if not ok:
         print("Error in TakeMeasurement()")
         return False

    if not hasTouched:
         print("Error Confirming first measurement to side of table - did not touch")
         return False

    print("Table measured at :"+str(measureAngle))

    if (abs(measureAngle - servoPositionC) < 3):
        ok = True
        print("ConfirmFirstMeasureToSideOfTable() - done")
    else:
        ok = False
        print("ConfirmFirstMeasureToSideOfTable() - failed")
    
    return ok

def Nudge():
    print("Nudge?")
    time.sleep(1.0)
    while True:
        CheckEBreak()
        if button14.value == False:
            time.sleep(0.2)
            while button14.value == False:
                StepTableDownOneStepWithDelay()
                time.sleep(0.05)
            return

def RotateDownToFirstTouch():
    # Just move roughly doing measurements until we find the stick
    for stepCount in range(100):
        for _ in range(26):
            CheckEBreak()
            StepTableDownOneStepWithDelay()
        
        ok, hasTouched, measureAngle = TakeMeasurement()
        if not ok:
            print("Error in TakeMeasurement()")
            return False
        if hasTouched and measureAngle < 133:
            return True
    
    return False


def StepNextChunkAndTakeMeasurement(stepsToChunk,chunkNumber,rotationNumber):
    # Advance table down
    hasTouched = False

    # enable coils

    for _ in range(stepsToChunk):
        CheckEBreak()
        StepTableDownOneStepWithDelay()

        if TableIsAtLowerStop():
            print("Lower limit reached")
            Panic()
            return False, hasTouched
    
    # disable coils
    stepper_motor.release()

    # Take measurement
    ok, hasTouched, measureAngle = TakeMeasurement()
    if not ok:
        print("Error in TakeMeasurement()")
        return False, hasTouched
    print("%i:%i touched %s angle %s" % (rotationNumber,chunkNumber,str(hasTouched),str(measureAngle)))
    
    return True, hasTouched

def MakeOneFullRevolvePrintingAngles(rotationNumberForLeapStep):
    print("Revolution "+str(rotationNumberForLeapStep))
    
    hasTouchedInThisRevolution = False

    # A series of chunks makes up a revolution (chunks are not quite uniform divisions)
    chunk = 0
    # 44 lots of 26 steps
    #  6 lots of 27 steps
    #  1 lot of 27 + (1 if rev % 3 = 0) which adds the .3
    for stepCount in range(44):
        ok, hasTouched = StepNextChunkAndTakeMeasurement(26,chunk,rotationNumberForLeapStep)
        if hasTouched:
            hasTouchedInThisRevolution = True
        chunk = chunk + 1
        if not ok : return False

    for stepCount in range(6):
        ok, hasTouched = StepNextChunkAndTakeMeasurement(27,chunk,rotationNumberForLeapStep)
        if hasTouched:
            hasTouchedInThisRevolution = True
        chunk = chunk + 1
        if not ok : return False
            
    if rotationNumberForLeapStep % 3 == 0 :
        ok, hasTouched = StepNextChunkAndTakeMeasurement(27,chunk,rotationNumberForLeapStep)
        if hasTouched:
            hasTouchedInThisRevolution = True
        chunk = chunk + 1
        if not ok : return False
    else:
        # Lead step for sync
        ok, hasTouched = StepNextChunkAndTakeMeasurement(28,chunk,rotationNumberForLeapStep)
        if hasTouched:
            hasTouchedInThisRevolution = True
        chunk = chunk + 1
        if not ok : return False
    
    return True, hasTouchedInThisRevolution

def PerformScan():
    print("PerformScan")

    rotationCount = 0
    success = True

    while rotationCount < maxTableRevolutions:
        ok, hasTouchedInThisRevolution = MakeOneFullRevolvePrintingAngles(rotationCount)
        # If there was an error then stop
        if not ok:
            success = False
            break
        # If there were no measurements for a whole revolution then stop
        if not hasTouchedInThisRevolution:
            print("** INFO ** Did not touch object during previous revolution so stopping scan")    
            break
        rotationCount = rotationCount + 1

    print("PerformScan - done (revolutions %u",rotationCount)
    return True


def PokerHomeCycle():
    """Run the homing cycle for the poker

    Fully retract the poker to reset the sensor to open
    Move to near the table edge (doesn't matter on table height)
    Fully retract the poker to reset the sensor to open
    If all that gives the expected sensor readings then poker is home
    """

    print("Poker Homing")

    ok = FullyRetractPokerAndCheckSensor()
    if not ok : 
        print("** ERROR ** PokerHomeCycle() FullyRetractPoker() did not succeed")    
        return False
    time.sleep(1.0)
    print("Fully retract and confirm sensor reset - done")

    MovePokerToNearTableEdge()

    if PokerHasTouched():
        print("** ERROR ** PokerHomeCycle() When staging poker, touch sensor was triggered")    
        return False
    time.sleep(1.0)
    print("Stage Poker and confirm sensor available - done")

    ok = FullyRetractPokerAndCheckSensor()
    if not ok : 
        print("** ERROR ** PokerHomeCycle() FullyRetractPoker() did not succeed")    
        return False
    time.sleep(1.0)
    print("Fully retract poker ready for table movement - done")

    print("Poker Homed")
    return True


def PrepareThenPerformScan():
    """Runs the pre-scan homing cycles before and after the main scan

    This method homes the poke and the table and checks for errors.
    If there are no errors, it waits for button 14 to be pressed to confirm
    the scan. The scan is performed, then the table and the poker are homed
    again.
    """

    ok = FullyRetractPokerAndCheckSensor()
    
    if ok:
        ok = TableHomeCycle()

    if ok:
        ok = PokerHomeCycle()

    if ok:
        ok = ConfirmFirstMeasureToSideOfTable()
    
    if ok:
        ok = MoveTableToScanStartPosition()

    if ok:
        print("Press confirm to begin scan?")
        while True:
            CheckEBreak()
            # Wait for initialise, button 14...
            if button14.value == False:
                ok = PerformScan()

    if ok:
         ok = PokerHomeCycle()
    if ok:
        ok = TableHomeCycle()

    print("Done!")


CheckEBreak()
my_servo.angle = servoPositionB
servoCurrentTarget = servoPositionB

while True:

    # Wait for initialise, button 14...
    if button14.value == False:
        PrepareThenPerformScan()

    if button12.value == False:
        print("Lower limit switch is pressed")
        time.sleep(0.5)

    if button13.value == False:
        print("Upper limit switch is pressed")
        time.sleep(0.5)

    if photoSensorPin2.value == True:
        print("Photo sensor closed")
        time.sleep(0.5)
    
    CheckEBreak()

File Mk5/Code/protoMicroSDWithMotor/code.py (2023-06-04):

import time
import os
import adafruit_sdcard
import board
import busio
import digitalio
import storage
from digitalio import DigitalInOut, Direction, Pull
from adafruit_motor import stepper

print("MiroSD breakout with 28by test")
#adafruit_sdcard.mpy
#adafruit_bus_device

# Use any pin that is not taken by SPI
SD_CS = board.GP5

# It has a 1/64 reduction gear set and therefore moves in precise 512 steps per revolution
# Stepper motor setup
DELAY = 0.005  # fastest is ~ 0.004, 0.01 is still very smooth, gets steppy after that
STEPS = 512  # this is a full 360º
coils = (
    DigitalInOut(board.GP22),  # A1
    DigitalInOut(board.GP26),  # A2
    DigitalInOut(board.GP27),  # B1
    DigitalInOut(board.GP28),  # B2
)
for coil in coils:
    coil.direction = Direction.OUTPUT

stepper_motor = stepper.StepperMotor(
    coils[0], coils[1], coils[2], coils[3], microsteps=None
)

led = DigitalInOut(board.LED)
led.direction = Direction.OUTPUT
led.value = True

def blink(times):
    for _ in range(times):
        led.value = False
        time.sleep(0.1)
        led.value = True
        time.sleep(0.1)


# Use the filesystem as normal! Our files are under /sd

# This helper function will print the contents of the SD

def print_directory(path, tabs=0):
    for file in os.listdir(path):
        stats = os.stat(path + "/" + file)
        filesize = stats[6]
        isdir = stats[0] & 0x4000

        if filesize < 1000:
            sizestr = str(filesize) + " by"
        elif filesize < 1000000:
            sizestr = "%0.1f KB" % (filesize / 1000)
        else:
            sizestr = "%0.1f MB" % (filesize / 1000000)

        prettyprintname = ""
        for _ in range(tabs):
            prettyprintname += "   "
        prettyprintname += file
        if isdir:
            prettyprintname += "/"
        print('{0:<40} Size: {1:>10}'.format(prettyprintname, sizestr))

        # recursively print directory contents
        if isdir:
            print_directory(path + "/" + file, tabs + 1)



def stepper_fwd():
    print("stepper forward")
    for _ in range(STEPS):
        stepper_motor.onestep(direction=stepper.FORWARD)
        time.sleep(DELAY)
    stepper_motor.release()


while True:
        blink(10)
        stepper_fwd()
        time.sleep(0.2)
        print("Files on filesystem:")
        print("====================")
        print_directory("/sd")
        time.sleep(0.5)

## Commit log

2021-09-04 First steps with eyebolt. Nema stepper driven at 12V by rpi pico
    [Wiper01.stl]
2021-09-06 saving working separate examples
    [Wiper02.stl, Wiper03.stl]
2021-09-21 Saving a hole load of failed and WIP part designs.
    [HBlock01_withsupports.stl, HBlock02_withsupports.stl, MotorAttachement01.stl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]
2021-10-03 Loads of modelling and a bit of python
    [Bearing01.3mf, BearingUnderside01.3mf, DownwardLimitSwitchHolder.3mf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]
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2021-10-08 Loads of parts
    [8mmTestPart1.3mf, MidBridgeCentralStrut01.3mf, MidBridgeLower01.3mf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]
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2021-10-10 Added support part to top of driving cog. Code to perform first calibration measurement
    [UpperLimitSwitchHolder3.3mf, pinnion_top_brace.3mf, pinnion_top_brace_2.3mf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]
2021-10-10 Measuring is a bit slow. Can I read the value back off the servo?
    [TouchStickGuide.3mf, TouchStickGuide_2.3mf, TouchStickGuide_2b.3mf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]
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2021-10-10 measuring steps per revolution
    [Part1.3mf]
2021-10-31 Saving before writing new calibration script
    [Results.xlsx, Results3.xlsx, StickEndPart1.3mf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]
2021-12-01 investigating annoying servo issue using use01
    [Exp4Results.xlsx]
2022-01-16 All of Mark 1 moved into subfolder, Mk2 started.
    [8mmTestPart1.3mf, Bearing01.3mf, BearingUnderside01.3mf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]
2022-01-22 Mk2 files
    [Asm_RailStructure.cfg, BeltGripAfterWing03.3mf, BeltGripWithWing01.3mf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]
2022-01-23 Coding up BeltDriveHome testing python
    [ReturnNeedleBuffer01.stl, ShieldCableGuide.3mf, ShieldCableGuide_sizeGuide.3mf]
2022-02-20 Mark 2 calibrated and test scans
    [Carriage_04_TopGuides_03_forPTFE.3mf, Carriage_04_TopShim_01.3mf, Carriage_04_TopShim_02.3mf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]
2022-02-23 More calibration scans and scan of sorting hat.
    [CalibrationWallPart1.3mf]
2022-03-13 Working on Segmentation with data gathered using mkII with longer needle
    [Book1.xlsx, ReturnNeedleBuffer_7mm.3mf, TouchNeedlePart13.3mf]
2022-04-01 Start of MKIII design
    [UpperLimitSwitchHolderBaseStub01.3mf, UpperLimitSwitchHolderForBoxEnd01.3mf, planetAssembly.cfg]
2022-04-10 Parts and code for start of Mk3
    [Asm1.cfg, BeltGripAfterWing03.3mf, Carriage_04.3mf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]
2022-06-11 Updating MK4 to include thumbstick and new table.
    [ArmA_01.3mf, ArmA_02.3mf, ArmA_03.3mf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]
2022-07-29 Many additions to the mark 4.
    [BoltAdjusterTest01.3mf, CableGuides01.3mf, CableGuides02.3mf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]
2022-08-07 Calibration of beam movement
    [150x300_testBlock.3mf, LaserGripper02.3mf, LaserGripper03.stl]
2022-09-11 Loads more CAD for laser upgrade
    [250x400_testBlock.3mf, LaserLineGripper01.3mf, LaserLineGripper02.3mf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]
2022-09-11 Code for running the laser back an forth and checking it's alignment with the sensor.
2022-09-11 The new laser sensors seem to have reverse logic to the original unit - so I need to flip the photoSensorPin2 Value test.
    [code.py]
2022-09-11 Calibration results - worked less well than I hoped with round laser. Upgraded to line laser (hopefully an upgrade)
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2022-09-12 MIssed from last commit?
    [new_table_to_take_old_hub_04.3mf]
2023-01-13 New home button
    [SideMountBCombinedPlate01_RefCopy.3mf, SideMountBCombinedPlate02_RefCopy.3mf]
2023-04-01 Transferring to Mac
    [PrototypeInnerGearFull01.x_t]
2023-04-01 New parts for Camera module
    [mount_support0.3mf]
2023-04-18 Parts for Nema driven table and 28BYJ
    [140_teeth.dxf, 140_teeth.stp, 180_teeth.dxf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]
2023-04-19 More parts for printing
    [BoardToClipAdaptor01.stp, BoardToClipAdaptor01_mirror.stp, BoardToClipAdaptor02_mirror.stp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]
2023-05-01 Capturing first light from the camera board.
    [BoxConnectedMotor01.stp, BoxConnectedMotor02.stp, BoxConnectedMotor03.3mf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]
2023-05-06 Now I can capture jpg, how big bitmap can I capture?
    [BoxFrameAsm1.cfg, LengthwiseBoxConnectedMotor02.3mf, LengthwiseBoxConnectedMotor03.3mf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]
2023-05-23 More parts
    [LengthwiseBoxConnectedMotor06.3mf]
2023-06-04 Added SD card on breadboard. Reprinted board support so I can add tie points for additional wires.
    [BoxTopClipForSDCard_01.stp, board_side_l_03.stp]
2023-06-04 code_06 - error read only file system
    [code.py]
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2023-06-04 Distortion is being correctly removed from a test image!
    [laptop.py]
2023-06-16 First attempt at high-res image capture is failure
    [code.py]
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2023-06-18 Not sure why this isn't comiting
    [BoxFrameAsm1.cfg, lazer_holder_02.3mf, lazer_holder_02.stp]
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2023-07-01 Code crashed pico. Saving and rebooting
    [TryingToMakeSense.xlsx]
2023-07-02 Can print from and edit _ratio_table
    [TryingToMakeSense.xlsx]
2023-07-02 This time I am correctly changing the size by redefining table values.
    [code.py]
2023-07-03 going to change my_camera_changeSize to run altered size on start-up
    [TryingToMakeSense.xlsx]
2023-07-04 Further changes
    [TryingToMakeSense.xlsx]
2023-07-08 Saving some more parts. Changes to tweak camera settings
    [BoxConnectedMotor_SideConnections_05.stp, BoxMotorSideBraceLink_02.stp, BoxMotorSideBraceLink_03.stp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]
2023-07-08 Changing to long exposure greatly improves noise problem
    [code.py]
2023-07-10 First 360 capture with new camera settings
    [BoxTopClip_ForEBreak.stp]
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2023-08-18 Dumping a load more images, and some revised 3d parts for blue laser and new turntable motor
    [BoxConnectedMotorAdaptor01.3mf, BoxFrameAsm1.cfg, BoxTopClip_JointForBlueLaser01.3mf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]
2023-08-18 More parts for lazer hinges and new motor and turntable. Videos for next update
    [BoxConnectedMotorAdaptor02.3mf, BoxConnectedMotorAdaptor03.3mf, MotorMountStiffener_01.3mf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]
2023-08-19 Working on color bar on edge of wheel
    [lazer_holder_red_angle_06.3mf]
2023-09-04 Designs for worm-gear and testing of direct drive revolutions
    [MotorSpaceBearingHolder02.3mf, MotorSpaceBearingHolder02_test.3mf, Rotary04.3mf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]
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2023-09-09 Saving data from production of worm drive pre-testing
    [AsmForWorm1.cfg, BoxFrameAsm1.cfg, LED_Strip_trough_01.3mf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]
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
